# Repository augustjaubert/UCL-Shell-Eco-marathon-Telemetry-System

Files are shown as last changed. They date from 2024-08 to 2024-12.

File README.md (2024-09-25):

# UCL Shell Eco-marathon Telemetry System

This system is designed to record, store, and evaluate the performance of a the prototype in real-time and post-race.

A system user guide can be found [here](https://augusts-organization-4.gitbook.io/telemetry-system-handbook).

Fork this repository to iterate on it and continue building the telemetry system.

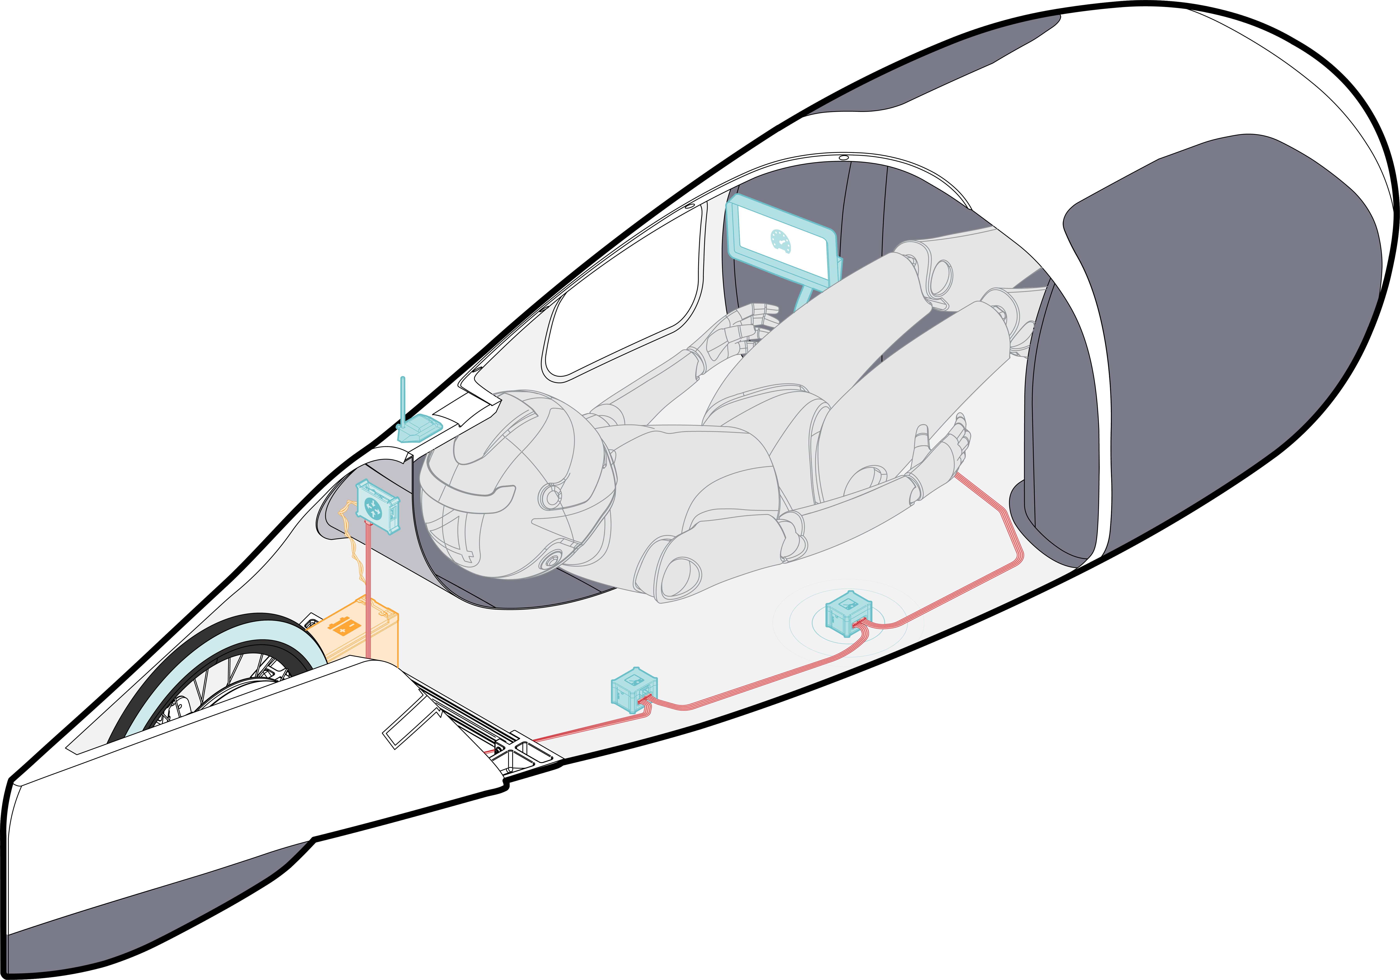
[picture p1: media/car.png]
System diagram


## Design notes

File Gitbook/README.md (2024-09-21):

# Overview

This user manual provides the information necessary for students to use the telemetry system.

<figure><figcaption></figcaption></figure>

### Features

This system was developed for usage on a race vehicle, to collect key performance indices. These vary depending on the vehicle competition, and this guide is directed towards the use on a vehicle participating in the Shell Eco Marathon competition.

It has,

* Expandable plug-in sensor capabilities
* CAN bus communication
* Data logging
* Live radio telemetry
* Driver & Race engineer graphical user interface

The system comprises of sensors, a receiver, and a radio station.

The sensors are configured as nodes on the CAN bus, meaning they each are paired with a small computer board. The latter acts as the middleman between the sensor’s interfacing protocol (i.e. the language the sensor talks in) and the CAN bus (i.e. what the telemetry system talks in).

The receiver is a computer board, who’s only function is to receive those sensor messages, store them onto a microSD card and handle the radio.

Notice that the receiver does not take care of the driver display. This is because depending on the setups, they may be at the complete opposite ends of a vehicle, so running a long cable from one to the other is not ideal. Instead, the system was designed so that any interfacing element (e.g. display, servo motor, etc.) can be attached to the CAN bus via a node and from there communicate with the system however it was programmed to.

The radio station is connected by USB to a computer, and all it does is intercept data over radio from the vehicle’s receiver, parse and translate that information, and then the computer program takes care of nicely displaying it all.

### Live race engineer interface

The live race engineer interface allows for the race engineer to assess the vehicle’s and driver’s performance during testing and at the race. This analysis is done via the use of plots. Currently there are three plots showing velocity, voltage, and current (these plots were meant to be used with a hydrogen powertrain). Besides the plots, there are toggle switches allowing for the comparison of various measured data (eg. Super-capacitor voltage and DC-DC voltage) and various laps.

The how to use section describes how the already existing application can be used for data analysis. While the how to edit/update section details how the application was setup and how to modify it or update it for future applications. Finally, the future work section mentions improvements that can be made.

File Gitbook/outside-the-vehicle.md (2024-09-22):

# Outside the vehicle

## Radio Station

### Setup

#### Hardware

1. Assembling the radio station with casing.
2. Attach the radio antenna to the station and USB connector to your laptop.

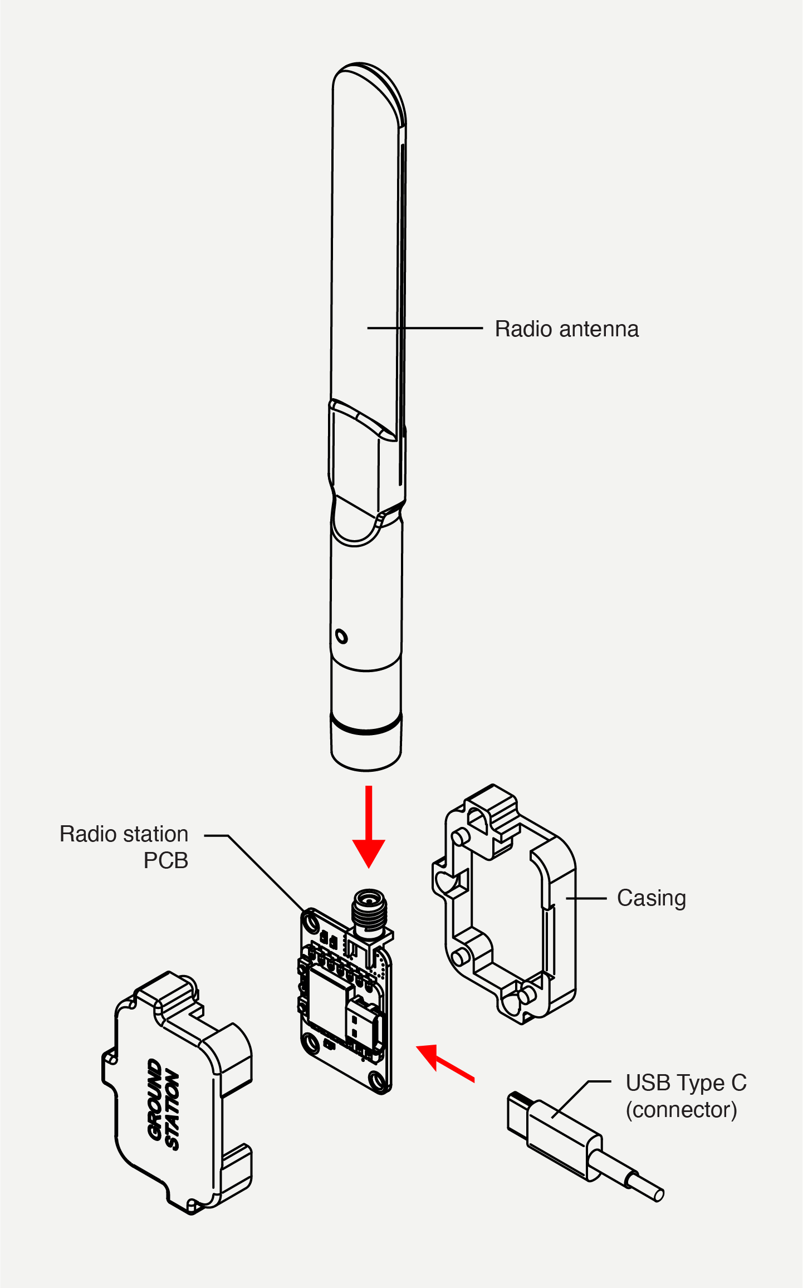
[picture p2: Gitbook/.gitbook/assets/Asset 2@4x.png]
<figure><figcaption></figcaption></figure>

#### Software

The radio station uses the Arduino IDE just like the other boards, and will need the RadioHead library installed from the github repository.

Before using the interface two applications need to be installed:

1\.        MATLAB for using the custom app.

2\.        VSCode (or any IDE) and the [Teleplot](https://github.com/nesnes/teleplot) extension installed for troubleshooting and redundancy.

### How to use

#### Software - Live Race Engineer Interface

1. Ensure that the telemetry system is turned on. Can be verified by lights on the boards and the driver display should be displaying information if connected.
2. Connect the ground station to your laptop.
3. Open Teleplot and select the port and baudrate (115200 by default).
4. Use the Teleplot interface to verify that data is being received and monitor it.
5. If Teleplot worked, disconnect from it (only one application can access a given serial port at a time) open the MATLAB application and run it.
6. On the top left of the MATLAB application select the port and baudrate (same as Teleplot).
7. If this worked successfully  you should be seeing data being plotted on the plots. Use the lap and quantity toggle switched to adjust the plots.

{% hint style="warning" %}
* Always start with Teleplot.
* The data that is being sent from the ground station to the laptop follows the format specified by Teleplot A:B§C
  * **A** is the name of the telemetry variable (be kind and avoid `:|` special chars in it!).
  * **B** is either the integer or floating point value to be plotted or a text format value to be displayed.
  * **C** is **optional** and is the unit of the telemetry ( please avoid `,;:|.` special chars in it!).
* The MATLAB application will crash if you click on a toggle switch that has no datafeed assigned to it.
* The timer in the MATLAB application currently needs to be started manually.
{% endhint %}

### Development

#### How to edit/update

The MATLAB application works by taking reading the next message from the serial port which contains a single measurement in the Teleplot format, identifying its quantity (eg. Velocity, Super-capacitor voltage), storing it to it’s corresponding cell array (an array of arrays more detail on it later), and updating the plots accordingly with the new data while also checking which checkbox is checked.

{% hint style="info" %}
**Why cell arrays?**

Cell arrays were used to allow for various measurements per lap to be taken and stored in a dynamic structure. Where the index of the cell array corresponds to the lap number. Allowing to compare various laps measurements with each other based on measurement number. Meaning that you can only compare for example the 10th velocity measurement of lap 3 with lap 5 and not the velocity at 100 m from the start line of these laps. This is a big negative of the current version of the interface, but assuming that the vehicle has consistent lap times then this approach is acceptable. How to improve this is detailed in the future work.
{% endhint %}

#### Main bits of the code

Whenever calling a function in the MATLAB app environmnent the first value you need to pass into it is always “app”.

<details>

<summary>Cell arrays</summary>

This is where the readings will be stored as discussed previously.

{% code overflow="wrap" %}
```matlab
velocity = {}; %Cell array to store velocity readings of each lap
current = {}; %Cell array to store current readings of each lap
voltage = {}; %Cell array to store voltage readings of each lap
%Voltage values
superCapsOverallVoltage = {}; %Cell array to store the supercaps overall voltage readings of each lap
beforeMotorControlVoltage = {}; %Cell array to store the before motor control voltage readings of each lap
DCDCVoltage = {}; %Cell array to store the DC DC voltage readings of each lap
```
{% endcode %}

</details>

<details>

<summary>Start-up function</summary>

This is the function that allows for the serial port readings to be continuously (= every 1 ms) monitored and updated (highlighted in yellow), ultimately enabling the plots to be updated. The other stuff named timer are used to update the stopwatch.

Define these in `properties (Access = private)`

<pre class="language-matlab" data-overflow="wrap"><code class="lang-matlab">        <a data-footnote-ref href="#user-content-fn-1">myTimer %Timer</a>
        Timer % Timer object
        TimerObject % Timer object
        StartTime % Start time
</code></pre>

Function itself

<pre class="language-matlab" data-overflow="wrap"><code class="lang-matlab">        function startupFcn(app)
            % Query available serial ports
            serialInfo = serialportlist("available");
            app.serialPort.Items = serialInfo;
            if isempty(serialInfo)
                app.serialPort.Items = {'No Ports Available'};
                app.serialPort.Enable = 'off';
            else
                app.serialPort.Enable = 'on';
            end
            <a data-footnote-ref href="#user-content-fn-2">app.myTimer = timer('ExecutionMode', 'fixedRate', 'Period', 1, 'TimerFcn', @(src, event)myTimerCallback(app, src, event)); % Specify the callback function</a>
            % Start the timer
            start(app.myTimer);
            app.TimerObject = timer(...
                'ExecutionMode', 'fixedRate', ...
                'Period', 1, ... % Update every second
                'TimerFcn', @(~,~)updateTimer(app));
        end
</code></pre>

</details>

As of now the way the code is setup you need to define a new add value function for each quantity that you want to be plotted and a function to update each of your plots.

<details>

<summary>Adding the new values</summary>

The function works by appending the value you give it to the end of the nth array in the cell array. Where n is the current lap number.

{% code overflow="wrap" %}
```matlab
        function addVelocityValue(app, value)
            lapIndex = app.LapField.Value; % Get the current lap index from the LapField
    
            if length(app.velocity) < lapIndex || isempty(app.velocity{lapIndex})
                % If the current lap's cell doesn't exist, initialize it with the value
                app.velocity{lapIndex} = value;
            else
                % Otherwise, append the value to the existing cell data
                app.velocity{lapIndex} = [app.velocity{lapIndex}, value];
            end
        end
```
{% endcode %}

</details>

<details>

<summary>Plotting the new values</summary>

_Single variable plots_ - For plots like velocity where you are only comparing its value through various laps the following function was created to plot it.

{% code overflow="wrap" %}
```matlab
        function updateVelocityPlot(app)
            cla(app.velUIAxes);  % Clear the current axes
            hold(app.velUIAxes, 'on');
            checkedNodes = app.LapTree.CheckedNodes;  % Get the list of checked nodes

            % Loop over each checked node
            for i = 1:numel(checkedNodes)
                node = checkedNodes(i);  % Get each checked node
                lapIndex = node.NodeData;  % Assuming NodeData stores the corresponding lap index

                % Ensure lapIndex is valid and within bounds
                if isnumeric(lapIndex) && lapIndex > 0 && lapIndex <= length(app.velocity)
                    % Check if the lap data exists and is not empty
                    if ~isempty(app.velocity{lapIndex})
                        plot(app.velUIAxes, app.velocity{lapIndex}, 'DisplayName', sprintf('Lap %d', lapIndex), 'LineWidth',4);
                    end
                end
            end
            hold(app.velUIAxes, 'off');
            legend(app.velUIAxes, 'Location', 'best');
            title(app.velUIAxes, 'Velocity vs Measurements');
            xlabel(app.velUIAxes, 'Measurements');
            ylabel(app.velUIAxes, 'Velocity (m/s)');
        end

```
{% endcode %}

***

_Multivariable plots_ - For plots where multiple quantities are being compared within a lap and over various laps the following function can be used. With the difference compared to the previous function being the switch which checks for which quantities should be plotted for the given lap.

{% code overflow="wrap" %}
```matlab
        function updateCurrentPlot(app)
            cla(app.currentUIAxes);  % Clear the current axes
            hold(app.currentUIAxes, 'on');
            checkedLapNodes = app.LapTree.CheckedNodes;  % Get the list of checked nodes from the LapTree
            checkedCurrentParameters = app.CurrentTree.CheckedNodes;  % Get the list of checked voltage parameters

            % Loop over each checked lap node
            for i = 1:numel(checkedLapNodes)
                lapNode = checkedLapNodes(i);  % Get each checked lap node
                lapIndex = lapNode.NodeData;  % Assuming NodeData stores the corresponding lap index

                % Ensure lapIndex is valid and within bounds
                if isnumeric(lapIndex) && lapIndex > 0 && lapIndex <= length(app.velocity)
                    % Check if the lap data exists and is not empty

                    % Loop over each checked parameter node
                    for j = 1:numel(checkedCurrentParameters)
                        parameterNode = checkedCurrentParameters(j);
                        parameterIndex = parameterNode.NodeData;  % NodeData here should correspond to the parameter index

                        switch parameterIndex
                            case 1  % Supercaps Overall Current
                                if ~isempty(app.superCapsOverallCurrent{lapIndex})
                                    plot(app.currentUIAxes, str2double(app.superCapsOverallCurrent{lapIndex}), 'DisplayName', sprintf('SCO Lap %d', lapIndex), 'LineWidth',4);
                                end
                            case 2  % Supercaps Charge Current
                                if ~isempty(app.superCapsChargeCurrent{lapIndex})
                                    plot(app.currentUIAxes, str2double(app.superCapsChargeCurrent{lapIndex}), 'DisplayName', sprintf('SCC Lap %d', lapIndex), 'LineWidth',4);
                                end
                            case 3  % Before Motor Control Current
                                if ~isempty(app.beforeMotorControlCurrent{lapIndex})
                                    plot(app.currentUIAxes, str2double(app.beforeMotorControlCurrent{lapIndex}), 'DisplayName', sprintf('BMC Lap %d', lapIndex), 'LineWidth',4);
                                end
                            % case 4  % DC DC Current
                            %     if ~isempty(app.DCDCCurrent{lapIndex})
                            %         plot(app.currentUIAxes, str2double(app.DCDCCurrent{lapIndex}), 'DisplayName', sprintf('DCDC Lap %d', lapIndex), 'LineWidth',4);
                            %     end
                        end
                    end
                end
            end
            hold(app.currentUIAxes, 'off');
            legend(app.currentUIAxes, 'Location', 'best');
            title(app.currentUIAxes, 'Current vs Measurements');
            xlabel(app.currentUIAxes, 'Measurements');
            ylabel(app.currentUIAxes, 'Current (A)');
        end
```
{% endcode %}

</details>

#### Putting it all together

{% hint style="info" %}
You can click on the underlined code to reveal information about its use.
{% endhint %}

<pre class="language-matlab" data-overflow="wrap" data-line-numbers data-full-width="true"><code class="lang-matlab"><a data-footnote-ref href="#user-content-fn-3">function myTimerCallback(app, src, event)</a>
            <a data-footnote-ref href="#user-content-fn-4">if (src.NumBytesAvailable > 0)</a>
                        <a data-footnote-ref href="#user-content-fn-5">dataStr = readline(src);  % Reads data from the serial port until a newline is received</a>
                        % Remove non-ASCII characters except '§'
                        <a data-footnote-ref href="#user-content-fn-6">dataStr = regexprep(dataStr, '[\s>]|[^\x20-\x7E§]', '');</a>
                        <a data-footnote-ref href="#user-content-fn-7">try</a>
                            % Split the data into its components
                            <a data-footnote-ref href="#user-content-fn-8">splitData = strsplit(dataStr, '§');  % Split based on the '§' delimiter</a>
                            <a data-footnote-ref href="#user-content-fn-9">if numel(splitData) == 2</a>
                                <a data-footnote-ref href="#user-content-fn-10">varNameValue = splitData{1};</a>
                                %varUnit = splitData{2};

                                % Further split to separate variable name and value
                                <a data-footnote-ref href="#user-content-fn-11">nameValueSplit = strsplit(varNameValue, ':');</a>
                                    <a data-footnote-ref href="#user-content-fn-12">if numel(nameValueSplit) == 2</a>
                                        <a data-footnote-ref href="#user-content-fn-13">varName = nameValueSplit{1};</a>
                                        <a data-footnote-ref href="#user-content-fn-14">varValue = str2double(nameValueSplit{2});  % Convert value to double</a>

                                        <a data-footnote-ref href="#user-content-fn-15">if strcmp(varName, 'Lap#')</a>
                                            <a data-footnote-ref href="#user-content-fn-16">app.LapField.Value = varValue;</a>
                                            <a data-footnote-ref href="#user-content-fn-17">handleNewLap(app);</a>

                                        elseif strcmp(varName, 'Velocity')
                                            %disp('This is a velocity reading');
                                            <a data-footnote-ref href="#user-content-fn-18">addVelocityValue(app, varValue);</a>
                                            <a data-footnote-ref href="#user-content-fn-19">updateVelocityPlot(app);</a>

                                        %Supercaps Overall voltage update
                                        elseif strcmp(varName, 'SCOV')
                                            <a data-footnote-ref href="#user-content-fn-20">addSCOVoltageValue(app, string(varValue));</a>
                                            <a data-footnote-ref href="#user-content-fn-21">updateVoltagePlot(app);</a>

                                        %before motor control voltage update
                                        elseif strcmp(varName, 'BMCV')
                                            <a data-footnote-ref href="#user-content-fn-22">addBMCVoltageValue(app, string(varValue));</a>
                                            <a data-footnote-ref href="#user-content-fn-23">updateVoltagePlot(app);</a>

                                        %DC DC voltage update
                                        elseif strcmp(varName, 'DCDCV')
                                            <a data-footnote-ref href="#user-content-fn-24">addDCDCVoltageValue(app, string(varValue));</a>
                                            <a data-footnote-ref href="#user-content-fn-25">updateVoltagePlot(app);</a>

                                        %Supercaps Overall current update
                                        elseif strcmp(varName, 'Curr1')
                                            <a data-footnote-ref href="#user-content-fn-26">addSCOCurrentValue(app, string(varValue));</a>
                                            <a data-footnote-ref href="#user-content-fn-27">updateCurrentPlot(app);</a>

                                        %Supercaps Charge current update
                                        elseif strcmp(varName, 'Curr2')
                                            <a data-footnote-ref href="#user-content-fn-28">addSCCCurrentValue(app, string(varValue));</a>
                                            <a data-footnote-ref href="#user-content-fn-29">updateCurrentPlot(app);</a>

                                        %Before Motor Control Current
                                        %update
                                        elseif strcmp(varName, 'Curr3')
                                            <a data-footnote-ref href="#user-content-fn-30">addBMCCurrentValue(app, string(varValue));</a>
                                            <a data-footnote-ref href="#user-content-fn-31">updateCurrentPlot(app);</a>

                                        %DC DC Current update
                                        elseif strcmp(varName, 'DCDCC')
                                            <a data-footnote-ref href="#user-content-fn-32">addDCDCCurrentValue(app, string(varValue));</a>
                                            <a data-footnote-ref href="#user-content-fn-33">updateCurrentPlot(app);</a>
                                        end
                                    else
                                        disp('Error: Variable name and value not in expected format.');
                                    end
                            else
                                    disp('Error: Data not in expected format.');
                            end
                        catch
                            disp(['Error processing data: ', dataStr]);
                        end
            end
        end
</code></pre>

### Future work

#### Live Race Engineer Interface

The interface can be improved upon by creating a sophisticated database structure and querying the data from it. This would allow for any kind of comparison plot to be created. Furthermore, instead of sending the measurements from the vehicle to the ground station they could be uploaded to an online database from which the readings can be accessed by any number of race engineers and from anywhere, allowing more people to do various kinds of data analysis simultaneously.

## Off-track data analysis

The following procedure applies to both hydrogen and battery electric MATLAB code, found on the Github repo.&#x20;

The code first runs an overview of the testing data with the lap-by-lap performance. Then, the user inputs the lap numbers to allow for comparison of laps. Using the battery testing data, the tyre analysis can be performed automatically afterwards.&#x20;

The hydrogen powertrain introduces further losses which I have not been able to estimate accordingly. In case of Hydrogen analysis, Milan can perform some simulations. His results can be plotted using the MilanPlots.mlx file.

Hydrogen and Battery Analysis Procedure:

1. Gather the testing data in excel and format it using the column order specific to each analysis. For this, please check the excel tables provided and match the title of the columns with the raw data from testing.

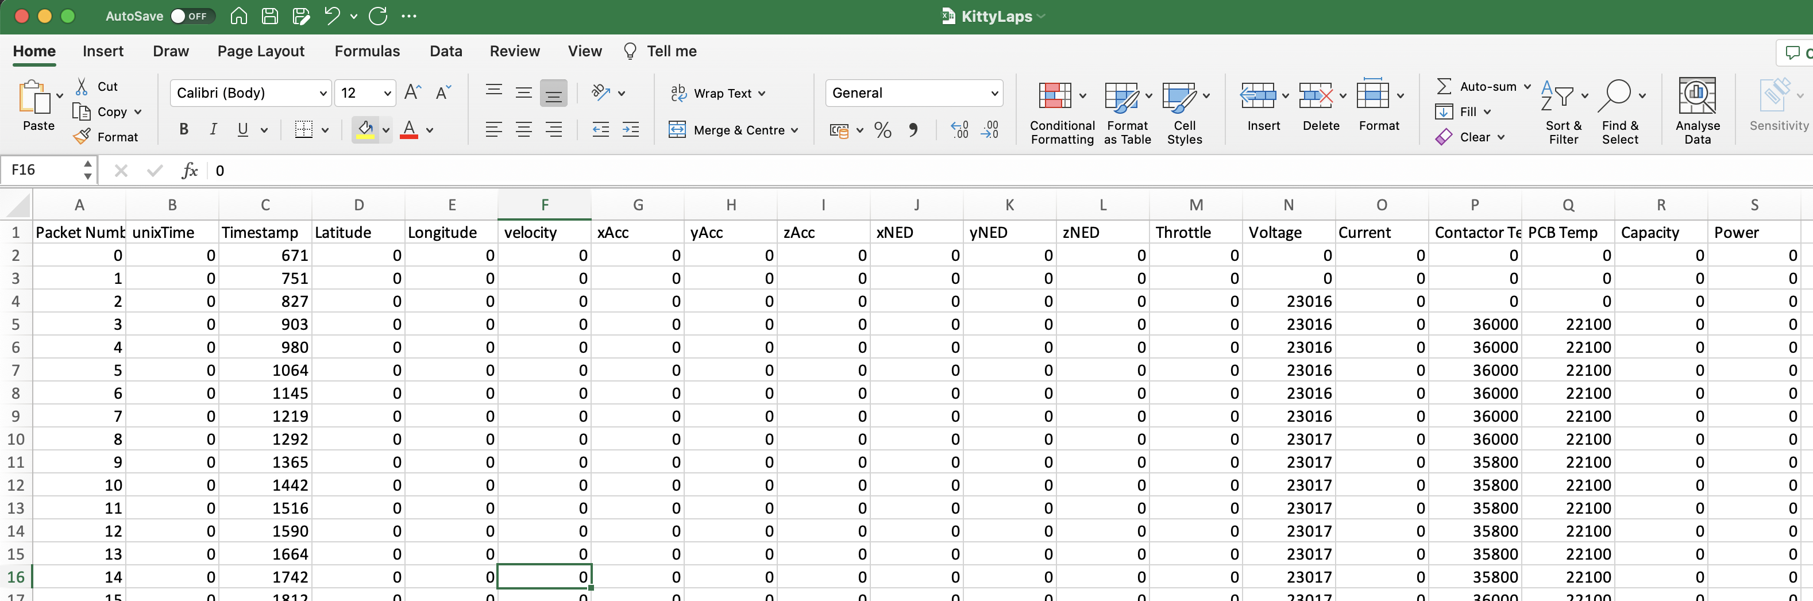
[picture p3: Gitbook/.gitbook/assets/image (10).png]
<figure><figcaption><p>Example of an excel sheet with telemetry data columns.</p></figcaption></figure>

{% hint style="info" %}
This data arrangement was specifically made for a hydrogen powertrain with the sensor mentioned in the [2024 configuration section](in-the-vehicle.md#id-2024-configuration).

If you are changing the sensors, you will need to modify the MATLAB code to account for that. Another (future work) solution is to make the plotting of the data automatic where if you upload a folder sectioned into multiple sensor folders from the receiver SD card,

e.g.&#x20;

* config (folder)
  * README.txt
* sensor 1 (folder)
  * telemetry\_date\_time.txt
* sensor 2 (folder)
  * telemetry\_date\_time.txt

... then the program will detect and plot a graph for each sensor folder.
{% endhint %}

2. Choose either the hydrogen or the electrical battery MATLAB code for analysis. In the first few lines, change the command to fit the correct file name: data = readtable('RandomName.xlsx');
3. Follow the command window and input the two lap numbers to allow for the comparison of laps.
4. All the results are now displayed. The next step is to run Milan Plots or the Tyre Analysis.

[^1]: A

[^2]: A

[^3]: Timer function callback, allows the plots to be continuously updated.

[^4]: Converts the Teleplot formatted measurement into VarName and VarValue.

[^5]: Converts the Teleplot formatted measurement into VarName and VarValue.

[^6]: Converts the Teleplot formatted measurement into VarName and VarValue.

[^7]: Converts the Teleplot formatted measurement into VarName and VarValue.

[^8]: Converts the Teleplot formatted measurement into VarName and VarValue.

[^9]: Converts the Teleplot formatted measurement into VarName and VarValue.

[^10]: Converts the Teleplot formatted measurement into VarName and VarValue.

[^11]: Converts the Teleplot formatted measurement into VarName and VarValue.

[^12]: Converts the Teleplot formatted measurement into VarName and VarValue.

[^13]: Converts the Teleplot formatted measurement into VarName and VarValue.

[^14]: Converts the Teleplot formatted measurement into VarName and VarValue.

[^15]: Checks whether VarName is “Lap#” and if so increments to lap number.

[^16]: Checks whether VarName is “Lap#” and if so increments to lap number.

[^17]: Checks whether VarName is “Lap#” and if so increments to lap number.

[^18]: Compares the VarName with the a predefined variable name and stores it VarValue to the corresponding cell array.

[^19]: Updates the plots.

[^20]: Compares the VarName with the a predefined variable name and stores it VarValue to the corresponding cell array.

[^21]: Updates the plots.

[^22]: Compares the VarName with the a predefined variable name and stores it VarValue to the corresponding cell array.

[^23]: Updates the plots.

[^24]: Compares the VarName with the a predefined variable name and stores it VarValue to the corresponding cell array.

[^25]: Updates the plots.

[^26]: Compares the VarName with the a predefined variable name and stores it VarValue to the corresponding cell array.

[^27]: Updates the plots.

[^28]: Compares the VarName with the a predefined variable name and stores it VarValue to the corresponding cell array.

[^29]: Updates the plots.

[^30]: Compares the VarName with the a predefined variable name and stores it VarValue to the corresponding cell array.

[^31]: Updates the plots.

[^32]: Compares the VarName with the a predefined variable name and stores it VarValue to the corresponding cell array.

[^33]: Updates the plots.

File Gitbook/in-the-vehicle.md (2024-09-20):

# In the vehicle

## Node

The sensors are configured as nodes on the CAN bus, meaning they each are paired with a small computer board. The latter acts as the middleman between the sensor’s interfacing protocol (i.e. the language the sensor talks in) and the CAN bus (i.e. what the telemetry system talks in).

The node computer hardware diagram is presented in the figure below.

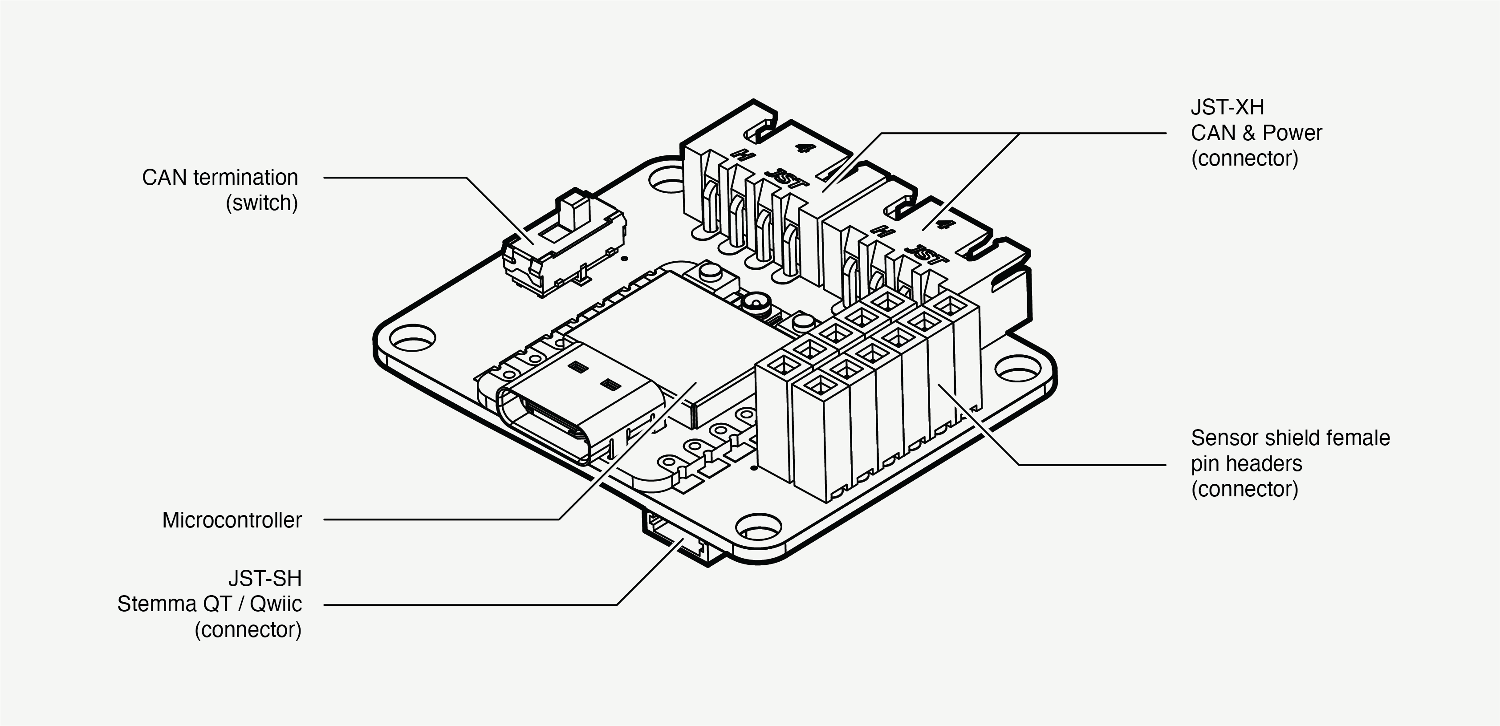
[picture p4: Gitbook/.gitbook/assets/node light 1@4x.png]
<figure><picture><source srcset=".gitbook/assets/node dark 1@4x.png" media="(prefers-color-scheme: dark)"></picture><figcaption></figcaption></figure>

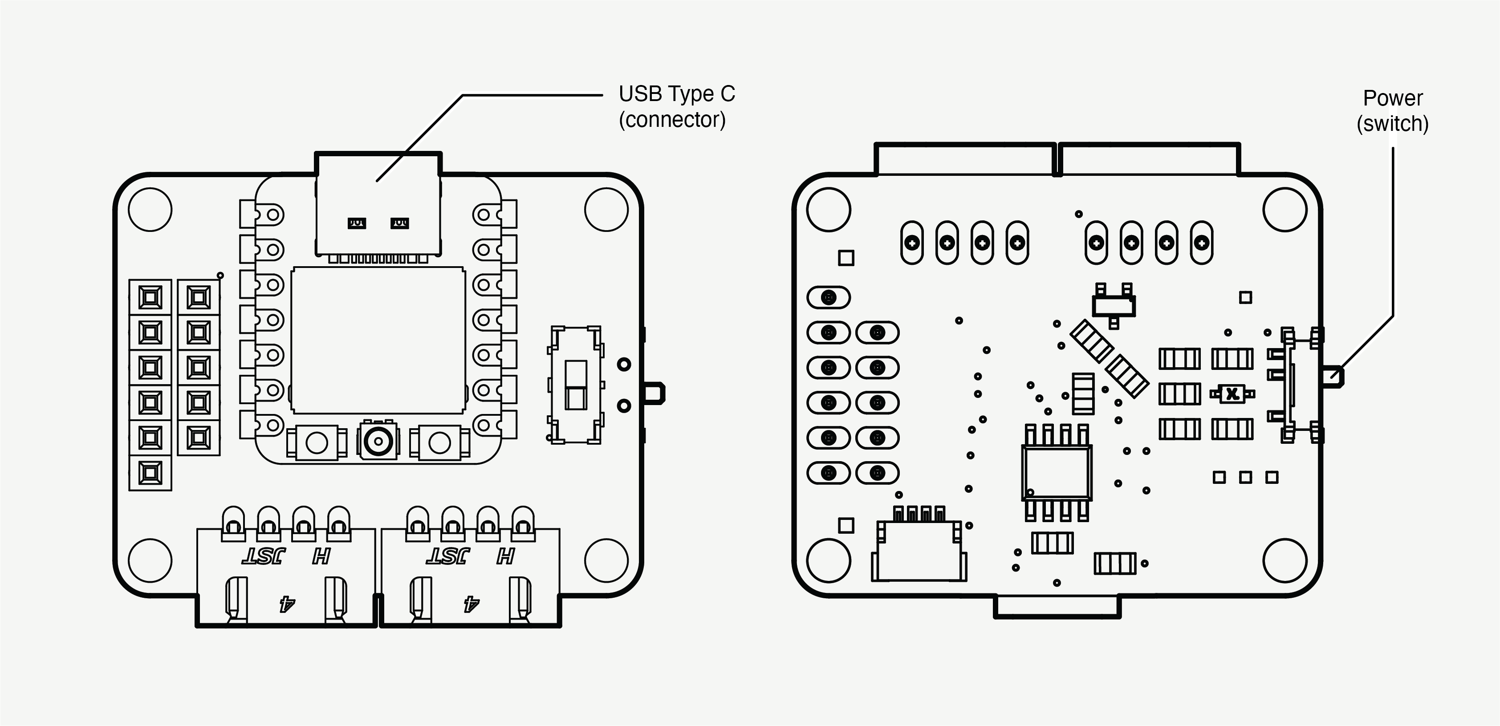
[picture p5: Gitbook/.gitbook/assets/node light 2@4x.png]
<figure><picture><source srcset=".gitbook/assets/node dark 2@4x.png" media="(prefers-color-scheme: dark)"></picture><figcaption><p>Technical diagrams of the node computer</p></figcaption></figure>

### Technical specs

{% tabs %}
{% tab title="Tech specs" %}
* The nodes use a ESP32 microcontroller (S3 or C3 models) from Espressif, manufactured by Seeed ([XIAO ESP32C3](https://wiki.seeedstudio.com/XIAO\_ESP32C3\_Getting\_Started/) / [XIAO ESP32S3](https://wiki.seeedstudio.com/xiao\_esp32s3\_getting\_started/)) (top surface).
* It uses two rows of 6 and 5 female headers (top surface) to connect to the sensor shield.
* A Qwiic / Stemma QT connector to connect to sensor breakout boards directly (no shield).
* They are equipped with [TCAN1462V-Q1](https://www.ti.com/lit/ds/symlink/tcan1462-q1.pdf?HQS=dis-mous-null-mousermode-dsf-pf-null-wwe\&ts=1698833597358) CAN transceivers (bottom surface) that make use of the MCU’s native [TWAI](https://docs.espressif.com/projects/esp-idf/en/stable/esp32/api-reference/peripherals/twai.html#overview) controllers.
* They have two daisy-chained 4-pin JST XH connectors (top surface) for the data transmission CAN High / Low, and the power pins from the Receiver +5V and GND.
* The slide switch on the top surface is the CAN termination switch, connecting the CAN High and Low lines by a 120 Ohm resistor.
* The CAN lines also have footprint for capacitors in series and parallel (bottom surface) to help if filtering is needed on the bus.
{% endtab %}

{% tab title="Pinout" %}
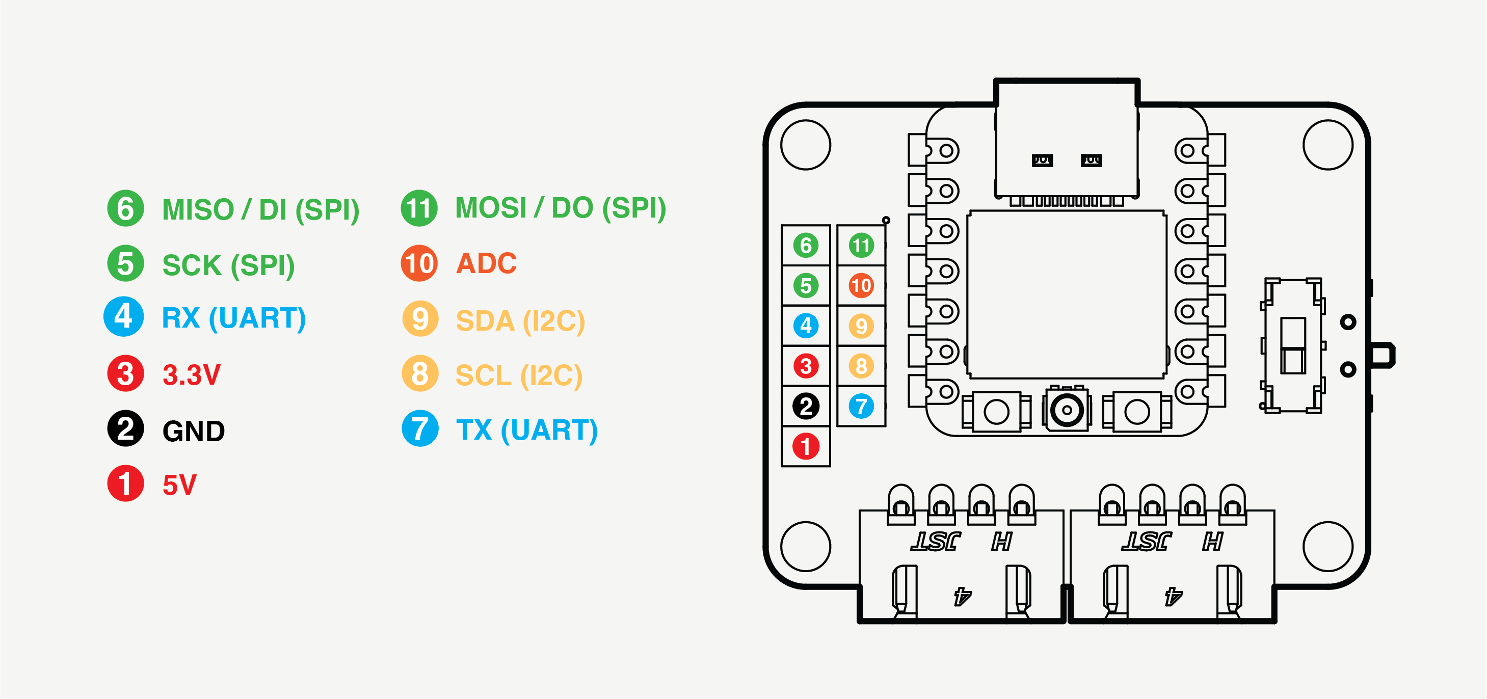
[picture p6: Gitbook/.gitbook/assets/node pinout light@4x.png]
<figure><figcaption></figcaption></figure>

{% hint style="info" %}
This pinout diagram is valid for the XIAO ESP32-C3 microcontrollers, but some pins also double as analog pins on the XIAO ESP32-S3 (see Table 1), marked as A\<Number> (e.g. A5).
{% endhint %}

<table><thead><tr><th width="154">pin #</th><th>C3 pinout</th><th>S3 pinout</th></tr></thead><tbody><tr><td>1</td><td>5V</td><td>5V</td></tr><tr><td>2</td><td>GND</td><td>GND</td></tr><tr><td>3</td><td>3.3V</td><td>3.3V</td></tr><tr><td>4</td><td>D7 / RX / GPIO20</td><td>D7 / RX / GPIO44</td></tr><tr><td>5</td><td>D8 / SCK / GPIO8</td><td>D8 / A8 / SCK / GPIO7</td></tr><tr><td>6</td><td>D9 / MISO / GPIO9</td><td>D9 / A9 / MISO / GPIO8</td></tr><tr><td>7</td><td>D6 / TX / GPIO21</td><td>D6 / TX / GPIO43</td></tr><tr><td>8</td><td>D5 / SCL / GPIO7</td><td>D5 / A5 / SCL / GPIO6</td></tr><tr><td>9</td><td>D4 / SDA / GPIO6</td><td>D4 / A4 / SDA / GPIO5</td></tr><tr><td>10</td><td>D3 / A3 / GPIO5</td><td>D3 / A3 / GPIO4</td></tr><tr><td>11</td><td>D10 / MOSI / GPIO10</td><td>D10 / A10 / MOSI / GPIO9</td></tr><tr><td>CAN_TX</td><td>GPIO_NUM_3</td><td>GPIO_NUM_2</td></tr><tr><td>CAN_RX</td><td>GPIO_NUM_4</td><td>GPIO_NUM_3</td></tr><tr><td>CAN_Standby</td><td>GPIO2</td><td>GPIO1</td></tr></tbody></table>
{% endtab %}
{% endtabs %}

### Setup

#### Hardware

1. Assembling the node case (in ascending order)

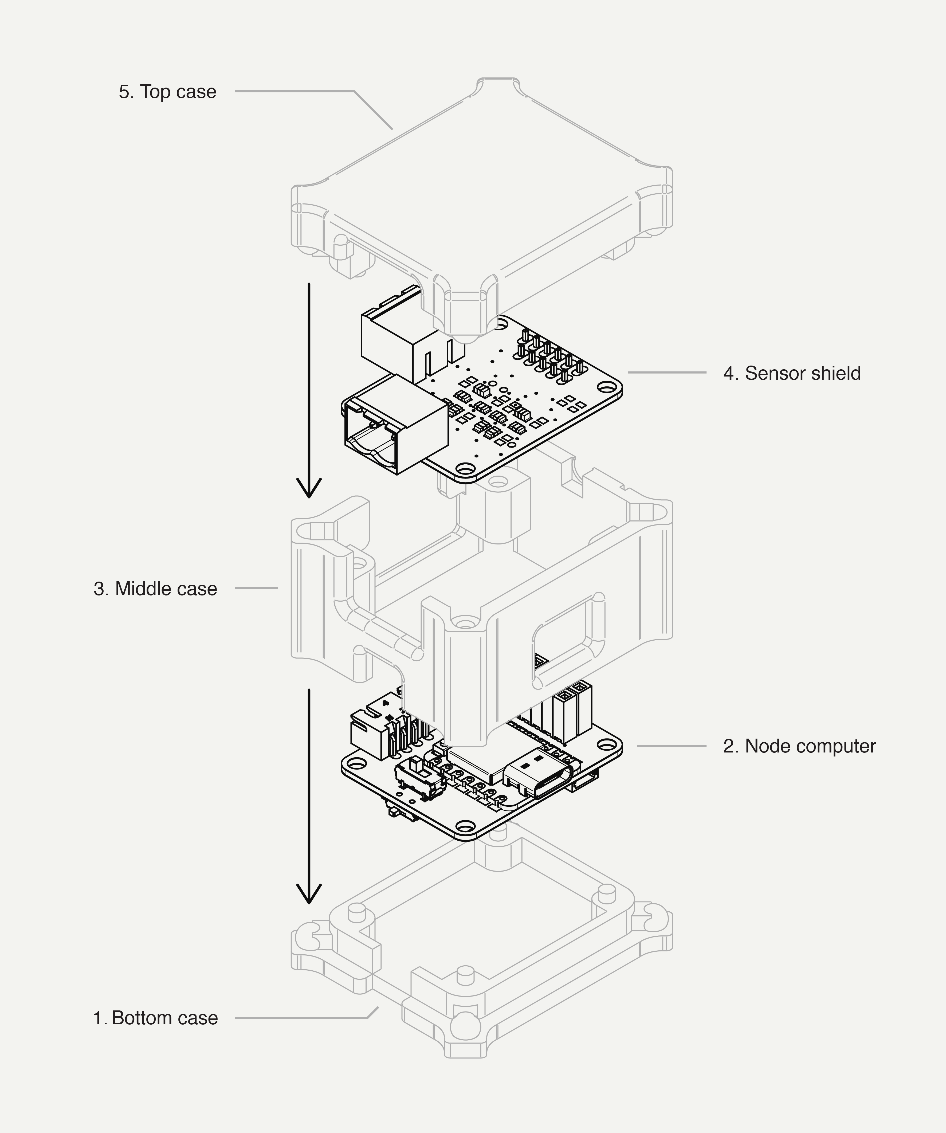
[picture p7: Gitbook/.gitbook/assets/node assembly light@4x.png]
<figure><figcaption></figcaption></figure>

{% hint style="info" %}
You can also connect sensor breakout boards that feature a Qwiic or Stemma QT connector from Adafruit and Sparkfun directly to the similar connector on the bottom surface. This is the case for the GPS node, which uses a Sparkfun breakout board.
{% endhint %}

2. Attaching the node to the CAN/Power bus

Connecting to the CAN and Power bus is easy. There are two 4-pin JST XH connectors opposite to the USB-C connector, which are connected in parallel for you to daisy-chain the whole system. This means that there’s no wrong way to connect it, just attach one cable to the bus, and if you want to add a new sensor, just attach another cable in the other connector and into the new node.

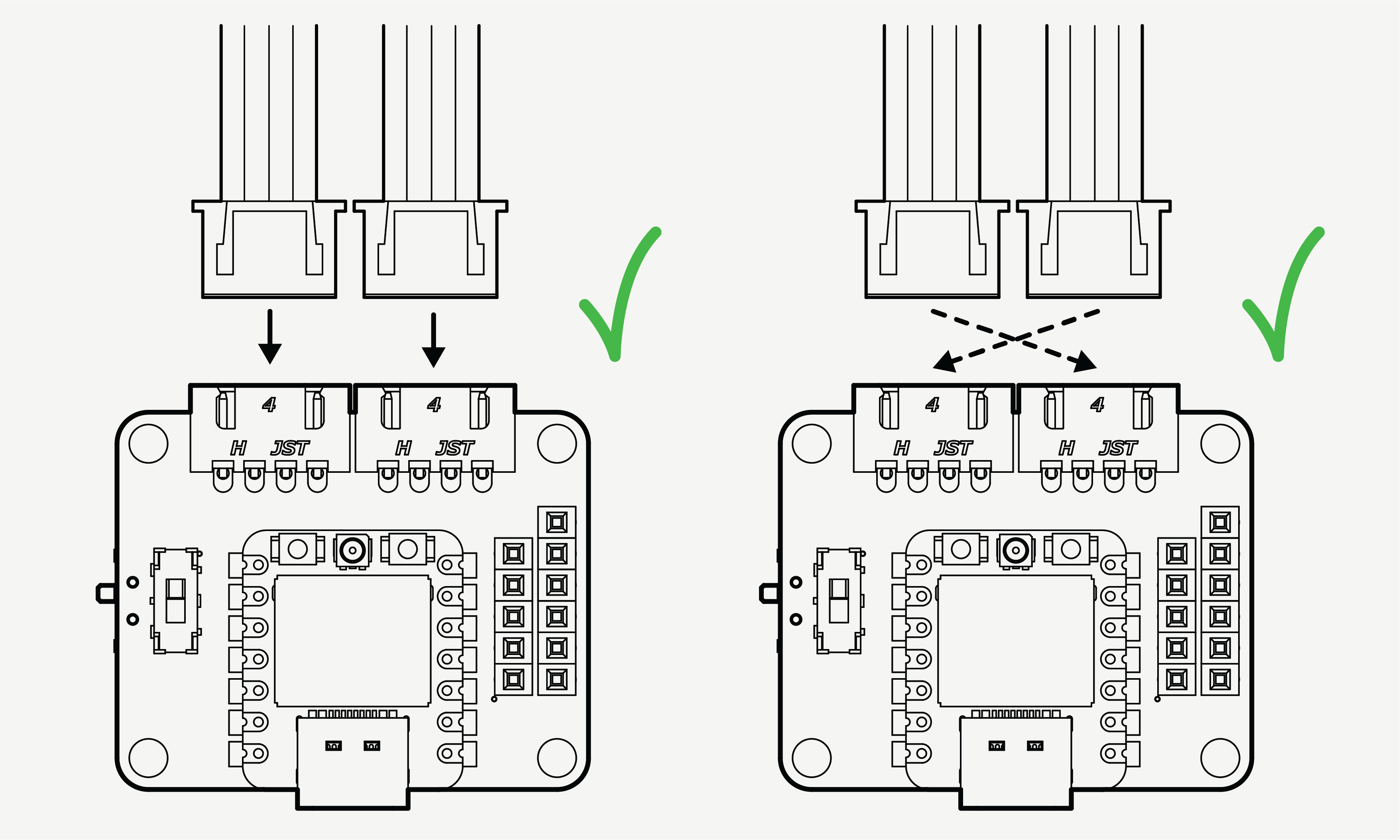
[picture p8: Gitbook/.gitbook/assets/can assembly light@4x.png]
<figure><picture><source srcset=".gitbook/assets/can assembly dark@4x.png" media="(prefers-color-scheme: dark)"></picture><figcaption></figcaption></figure>

3. Installing in the vehicle

Place the node wherever it is needed in the vehicle.

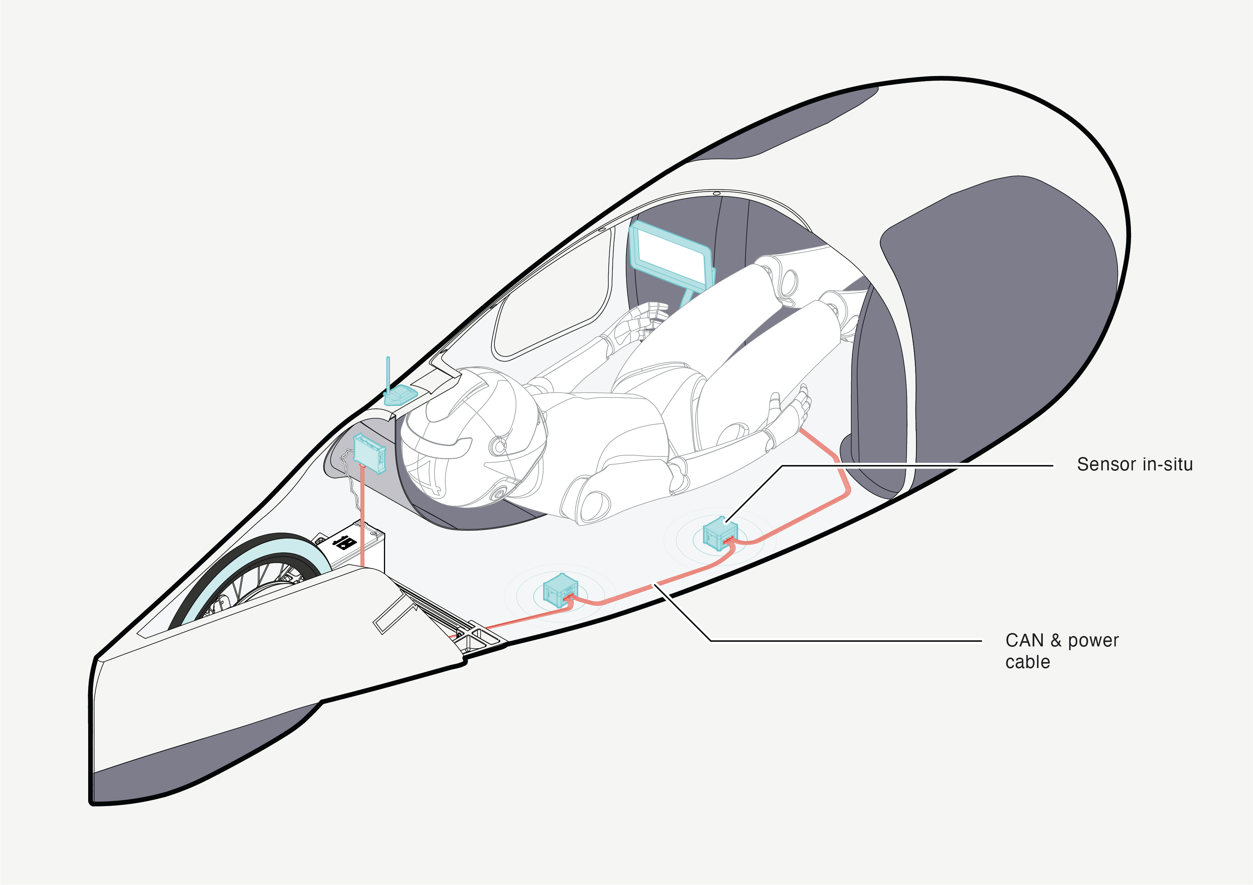
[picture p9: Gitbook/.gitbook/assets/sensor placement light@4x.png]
<figure><figcaption></figcaption></figure>

{% hint style="info" %}
If you need to make a new cable, make sure to use the proper connections as seen in the figure below.
{% endhint %}

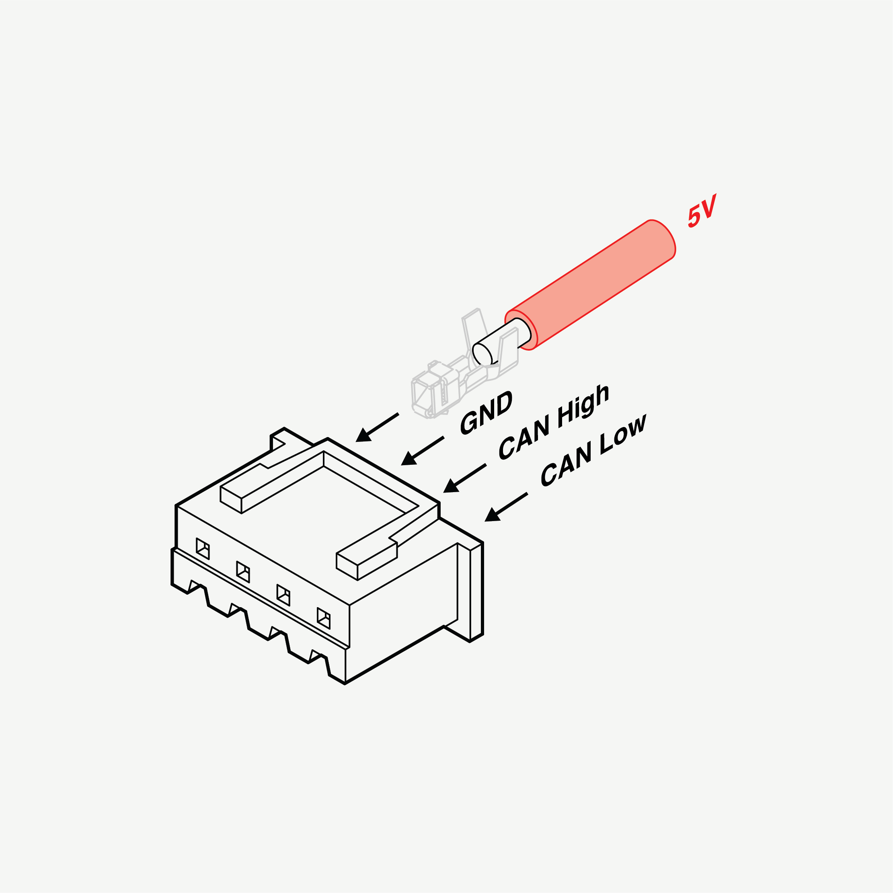
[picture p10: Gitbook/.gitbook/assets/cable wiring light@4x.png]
<figure><picture><source srcset=".gitbook/assets/cable wiring dark@4x.png" media="(prefers-color-scheme: dark)"></picture><figcaption><p>CAN &#x26; Power cable wiring diagram</p></figcaption></figure>

#### Software

1. Installing the integrated development environment (IDE)

The system works similar to most Arduino projects, as it has been coded in C++ using the Arduino IDE.

Any IDE will do the job, however we recommend using the following:

[Arduino IDE](https://www.arduino.cc/en/software) <mark style="color:orange;">is the easiest to use, has plenty of documentation and forum help and is sufficient almost 99% of the time.</mark>

[Platform IO](https://platformio.org/) (through VSCode) is essentially a pro version, where you have more control but requires a manual setup.

[ESP-IDF](https://docs.espressif.com/projects/esp-idf/en/stable/esp32/get-started/index.html#introduction) is the MCU's native IDE, which gives more liberty in using all its functions.

2. ESP board definitions

The ESP boards (MCU) are not defined by default in the Arduino IDE. You will have to add them initially to be able to connect to the nodes and others.

To do this in the Arduino IDE, navigate to **File > Preferences**, and fill **"Additional Boards Manager URLs"** with the url below: [_https://raw.githubusercontent.com/espressif/arduino-esp32/gh-pages/package\_esp32\_index.json_](https://raw.githubusercontent.com/espressif/arduino-esp32/gh-pages/package\_esp32\_index.json)

Navigate to **Tools > Board > Boards Manager...**, type the keyword "**esp32**" in the search box, select the latest version of **esp32**, and install it.

3. Installing the node library

Download the two files `Node.h` and `Node.cpp` from the [Github repository](https://github.com/augustjaubert/UCL-SEM-Telemetry-System) in the Node folder.

To add the node library to your arduino sketch[^1], simply add the two files in your sketch folder.

<details>

<summary>Example folder organisation</summary>

```
example_sketch (folder)
-> Node.cpp
-> Node.h
-> example_sketch.ino (arduino sketch)
```

</details>

4. Connecting to the node computer board

To connect the node computer to the arduino sketch, select the top-left text box **Select Board**.

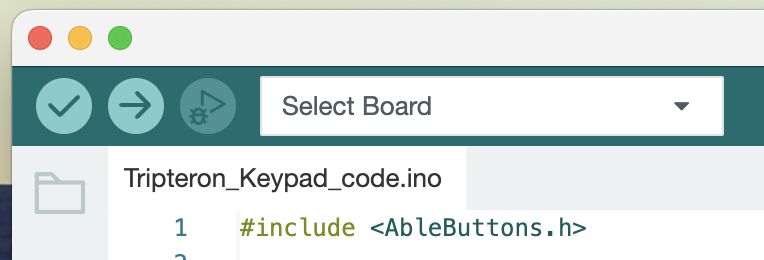
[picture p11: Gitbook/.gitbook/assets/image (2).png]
<figure><figcaption></figcaption></figure>

For C3 models - XIAO\_ESP32C3

For S3 models - XIAO\_ESP32S3

### How to use

Find the quick guide in the [overview section](./#quick-installation-guide).

{% hint style="info" %}
You can add up to 70+ nodes onto the CAN bus, however limiting the number of sensors to <15 is recommended (i.e. limit the different messages competing on the CAN bus).
{% endhint %}

#### Steps

1. Switch the node ON.

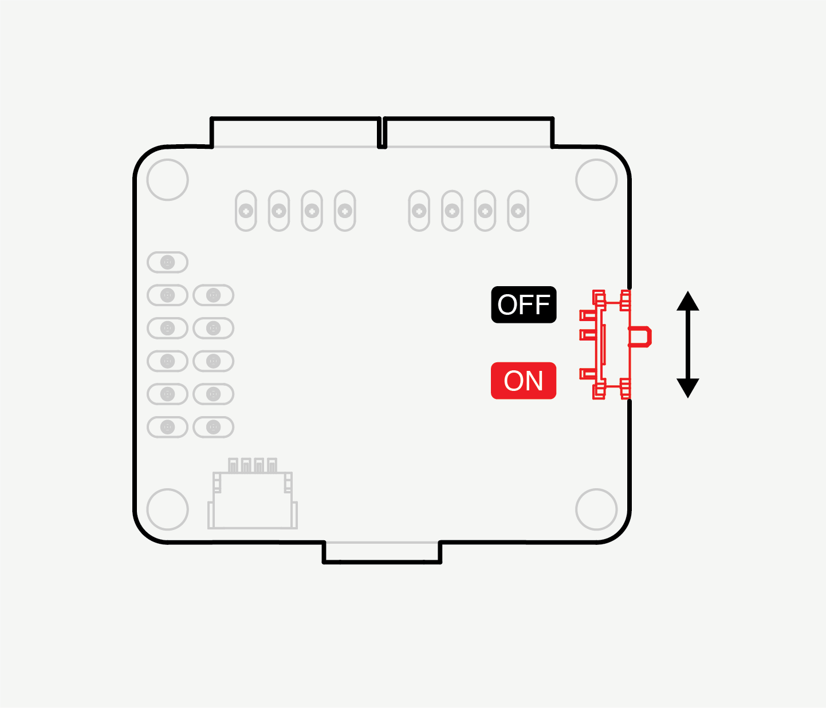
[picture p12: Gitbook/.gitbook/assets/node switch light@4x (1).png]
<figure><figcaption></figcaption></figure>

2. Assemble the node (sensor, computer and case).
3. Connect a CAN cable to one of the JST sockets to add the node on the CAN bus.
4. If the node is added at the end of the bus, switch the CAN termination ON<mark style="color:orange;">.</mark>

{% hint style="info" %}
After the system is powered, the node is powered if you see a LED lighting up.
{% endhint %}

{% hint style="warning" %}
Later versions of the node computer boards have a slide switch on the bottom, which need to be activated for the power rail to go through the board.&#x20;

Be careful because earlier versions have reversed ON/OFF writings by mistake, so if in doubt test it outside the vehicle, and if you see a blinking red/yellow light coming from the node, it is powered.
{% endhint %}

#### Troubleshooting

If it seems as though the Receiver is not seeing the sensor messages, or something else is not working as it should:

1. Disassemble the node.
2. Connect the node computer to your laptop through USB.
3. Open Arduino IDE, and check that you have the correct board definition in the top-left text box **Select Board**.

<figure><figcaption></figcaption></figure>

<details>

<summary>No board appearing</summary>

If you don't see a board appearing, then the MCU is not powered, or the serial connection has been severed. This can be because,

* The USB cable is not properly connected either to the node or laptop
* The MCU is not receiving power, which can be checked with a multimeter on the MCU pins to see if it detects a voltage. This can be due to a severed power connection on the circuit.
* The serial connection is severed, which can be because&#x20;
  * the USB connector on the MCU has been damaged,&#x20;
  * or because something (e.g. static electricity) has caused your laptop to disconnect the USB port (safety mode). It happens that connection is re-established after some time.
    * You can first try to reset the board by clicking the **RESET BUTTON** once while the board is connected to your PC. If that does not work, hold the **BOOT BUTTON**, connect the board to your PC while holding the **BOOT** button, and then release it to enter **bootloader mode**.

</details>

<details>

<summary>The wrong board is appearing</summary>

If the wrong board is appearing, that is a good sign because it recognises something.

You can open the text box, click on select **other board and port...** and search for the appropriate board.

The boards are,

For C3 models - XIAO\_ESP32C3

For S3 models - XIAO\_ESP32S3

S3 models are identifiable by the writing on the sticker and the presence of solderable pins on the bottom, as seen on the right side of the image below.

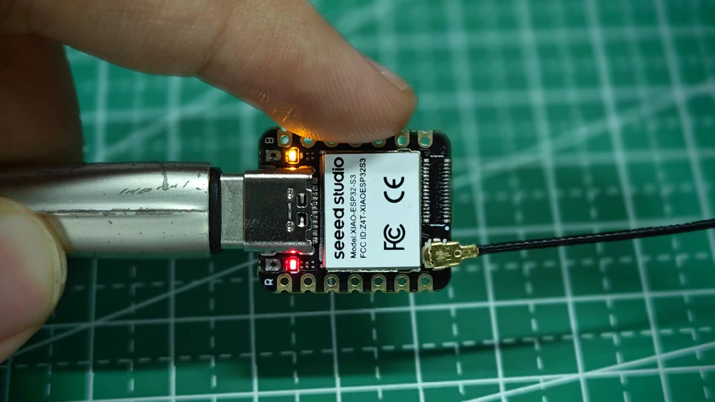
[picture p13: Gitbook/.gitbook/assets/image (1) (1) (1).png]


</details>

4. Open the serial monitor, in the top-right corner.

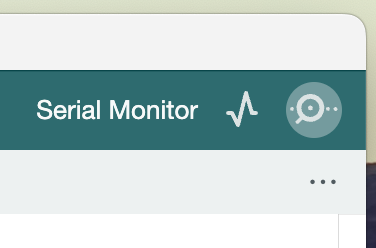
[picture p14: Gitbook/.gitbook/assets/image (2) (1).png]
<figure><figcaption></figcaption></figure>

This will present what is output on the serial port by the board, which you can use to deduce where the issues are coming from.

e.g. it can display "sensor not found on I2C bus" even when the sensor board is connected meaning that there is a connection issue between the node computer and sensor board).

{% hint style="info" %}
The serial output will only output things that it has been coded to output, so it is your responsibility to leave serial print commands in your code for debugging.
{% endhint %}

### Development

#### Node Library - to code a node

{% tabs %}
{% tab title="API reference" %}
* The `Node` class methods provide a high-level interface for interacting with a CAN bus network, abstracting away the complexities of direct hardware manipulation.
* The `VariableType` enumeration and `ExpectedMessage` structure facilitate the definition and handling of expected messages within the CAN network.

#### Usage Notes

* `uint32_t id`: The identifier of the expected message.
* `VariableType var1Type`: The type of the first variable in the message payload.
* `VariableType var2Type`: The type of the second variable in the message payload.

A structure representing an expected message with its identifier and variable types:

**`ExpectedMessage`**

* `INT32`: 32-bit signed integer.
* `UINT32`: 32-bit unsigned integer.
* `FLOAT`: Floating-point number.
* `NONE`: No variable (used when there is only one variable).

An enumeration defining the possible types of variables that can be included in a CAN message:

**`VariableType`**

12. `void initializeCANBus(gpio_num_t canRxPin, gpio_num_t canTxPin, uint8_t canStdbyPin, bool listenMode)`&#x20;
    * Initialises the CAN bus with the specified pins and mode.
13. `template <typename T> void convertToBytes(T value, byte *buffer)`&#x20;
    * Converts a value of type `T` to a byte array.

**Private Methods**

1. `void begin(gpio_num_t canRxPin = GPIO_NUM_NC, gpio_num_t canTxPin = GPIO_NUM_NC, uint8_t canStdbyPin = 0, bool listenMode = false)`
   * Initialises the CAN bus with the specified pins and mode.
2. `void initializeMessage(uint32_t id, uint8_t dataLength)`&#x20;
   * Initialises a message container with the specified ID and data length.
3. `void deleteMessage(uint32_t id)`&#x20;
   * Deletes a message from the `messages` container.
4. `template <typename T1, typename T2 = std::nullptr_t> void updateMessageData(uint32_t id, T1 var1, T2 var2 = nullptr)`&#x20;
   * Updates the data of a message with the given ID in the Node's message map.
5. `void transmitAllMessages(bool lowPowerMode = false, uint32_t sleepDurationMs = 1000)`&#x20;
   * Transmits all messages in the Node's message map to the CAN bus.
6. `void transmitMessage(uint32_t id, TickType_t ticks_to_wait = pdMS_TO_TICKS(1000))`&#x20;
   * Transmits a specific message with the specified ID and waits for the specified number of ticks.
7. `void addExpectedMessage(uint32_t id, VariableType var1Type)`&#x20;
   * Adds a single expected message with only one variable.
8. `void addExpectedMessage(uint32_t id, VariableType var1Type, VariableType var2Type)`&#x20;
   * Adds an expected message with two variables.
9. `void addExpectedMessages(const std::vector<ExpectedMessage> &messages)`&#x20;
   * Adds a collection of expected messages to the internal map.
10. `std::pair<uint32_t, std::pair<String, String>> parseReceivedMessage()`&#x20;
    * Parses the received CAN message and returns the message ID and string representations of the first and second variables in the message payload.
11. `void displayLatestMessageData()`&#x20;
    * Displays the data of the latest message in the Node's message map.

**Public Methods**

Creates an instance of the `Node` class.

```cpp
Node();
```

**Constructor**

**`Node`**

#### Classes and Structures

The `Node` library provides a framework for interacting with a CAN bus network using the ESP-IDF framework on ESP32 devices. It includes functionalities for initializing the CAN bus, sending and receiving messages, and managing message expectations.

The `Node` library provides a framework for interacting with a CAN bus network using the ESP-IDF framework on ESP32 devices. It includes functionalities for initializing the CAN bus, sending and receiving messages, and managing message expectations.

#### Classes and Structures

**`Node`**

**Constructor**

```cpp
Node();
```

Creates an instance of the `Node` class.

**Public Methods**

1. `void begin(gpio_num_t canRxPin = GPIO_NUM_NC, gpio_num_t canTxPin = GPIO_NUM_NC, uint8_t canStdbyPin = 0, bool listenMode = false)`
   * Initialises the CAN bus with the specified pins and mode.
2. `void initializeMessage(uint32_t id, uint8_t dataLength)`&#x20;
   * Initialises a message container with the specified ID and data length.
3. `void deleteMessage(uint32_t id)`&#x20;
   * Deletes a message from the `messages` container.
4. `template <typename T1, typename T2 = std::nullptr_t> void updateMessageData(uint32_t id, T1 var1, T2 var2 = nullptr)`&#x20;
   * Updates the data of a message with the given ID in the Node's message map.
5. `void transmitAllMessages(bool lowPowerMode = false, uint32_t sleepDurationMs = 1000)`&#x20;
   * Transmits all messages in the Node's message map to the CAN bus.
6. `void transmitMessage(uint32_t id, TickType_t ticks_to_wait = pdMS_TO_TICKS(1000))`&#x20;
   * Transmits a specific message with the specified ID and waits for the specified number of ticks.
7. `void addExpectedMessage(uint32_t id, VariableType var1Type)`&#x20;
   * Adds a single expected message with only one variable.
8. `void addExpectedMessage(uint32_t id, VariableType var1Type, VariableType var2Type)`&#x20;
   * Adds an expected message with two variables.
9. `void addExpectedMessages(const std::vector<ExpectedMessage> &messages)`&#x20;
   * Adds a collection of expected messages to the internal map.
10. `std::pair<uint32_t, std::pair<String, String>> parseReceivedMessage()`&#x20;
    * Parses the received CAN message and returns the message ID and string representations of the first and second variables in the message payload.
11. `void displayLatestMessageData()`&#x20;
    * Displays the data of the latest message in the Node's message map.

**Private Methods**

12. `void initializeCANBus(gpio_num_t canRxPin, gpio_num_t canTxPin, uint8_t canStdbyPin, bool listenMode)`&#x20;
    * Initialises the CAN bus with the specified pins and mode.
13. `template <typename T> void convertToBytes(T value, byte *buffer)`&#x20;
    * Converts a value of type `T` to a byte array.

**`VariableType`**

An enumeration defining the possible types of variables that can be included in a CAN message:

* `INT32`: 32-bit signed integer.
* `UINT32`: 32-bit unsigned integer.
* `FLOAT`: Floating-point number.
* `NONE`: No variable (used when there is only one variable).

**`ExpectedMessage`**

A structure representing an expected message with its identifier and variable types:

* `uint32_t id`: The identifier of the expected message.
* `VariableType var1Type`: The type of the first variable in the message payload.
* `VariableType var2Type`: The type of the second variable in the message payload.

#### Usage Notes

* The `Node` class methods provide a high-level interface for interacting with a CAN bus network, abstracting away the complexities of direct hardware manipulation.
* The `VariableType` enumeration and `ExpectedMessage` structure facilitate the definition and handling of expected messages within the CAN network.
{% endtab %}

{% tab title="Example sketch" %}
This example code initialises the CAN messages in the setup, and then in the loop updates them and sends them onto the bus.

```cpp
#include "Node.h"

/**
 * Pin Configuration for XIAO ESP32-C3 and XIAO ESP32-S3
 *
 * This section defines the GPIO pins used for TX, RX, and controlling
 * the sleep mode of the CAN transceiver chip based on the specific
 * board variant being used. Ensure that you select the correct pin
 * configuration for your hardware setup.
 *
 * TX_GPIO_NUM: Transmit Pin
 * - XIAO ESP32-C3: GPIO_NUM_3
 * - XIAO ESP32-S3 (e.g. Screen Node): GPIO_NUM_2
 *
 * RX_GPIO_NUM: Receive Pin
 * - XIAO ESP32-C3: GPIO_NUM_4
 * - XIAO ESP32-S3 (e.g. Screen Node): GPIO_NUM_3
 *
 * sleepPin: Sleep Control Pin for the CAN Transceiver
 * - XIAO ESP32-C3: 2
 * - XIAO ESP32-S3: 1
 *
 * Note:
 * - Make sure to define the correct board type before setting these pins.
 * - These configurations are critical for proper communication over the CAN bus.
 */

Node node;
void setup()
{
  // Begin serial communication at a baud rate of 115200.
  // This is necessary to print messages to the serial monitor.
  Serial.begin(115200);

  // Delay for 1 second to allow the serial monitor to initialize properly.
  // This is necessary to avoid interference with serial printing.
  delay(1000);

  // Initialize the node with the specified RX and TX pins, a standby pin, and a listen mode flag.
  // The node will use the specified pins for CAN communication.
  // The standby pin is used to control the CAN transceiver.
  // The listen mode flag determines whether the node will listen for messages on the CAN bus.
  node.begin(GPIO_NUM_4, GPIO_NUM_3, 2);

  // Initialize a message container with the specified ID and data length.
  // This function is called once per message ID that is used (i.e. to be sent or received).
  // The message container is used to store the message ID and the data associated with the message.
  node.initializeMessage(10, 8);

  // Initialize another message container with another ID and data length.
  node.initializeMessage(14, 4);

  // Display the data of the latest message in the Node's message map.
  // This function iterates through the messages in the Node's message map to find
  // the message with the highest ID, which is assumed to be the latest message.
  // It then prints the ID and data of the latest message.
  node.displayLatestMessageData();

  // Add multiple expected messages.
  // This vector contains ExpectedMessage objects that represent the expected messages received by the node.
  // Each ExpectedMessage object has an ID and two variable types.
  std::vector<ExpectedMessage> messages = {
      {20, INT32, FLOAT}, // Example of a message with two variables
      {24, UINT32, NONE}  // Example of a message with only one variable
  };

  // Add the expected messages to the Node's internal map of expected messages.
  node.addExpectedMessages(messages);
}

void loop()
{
  /*
   * In the example loop, we update and transmit messages.
   * We update message 10 with sine values of i and -i.
   * We update message 14 with the value -14.0.
   * We transmit all messages.
   * We delay for 1 second before the next iteration.
   */
  for (int i = 0; i < 314; i++)
  {
    // Update message 10 with sine values of i and -i.
    node.updateMessageData(10, (sin((float)i / 100)), (sin((float)-i / 100)));

    // Update message 14 with the value -14.0.
    node.updateMessageData(14, (float)-14);

    // Transmit all messages.
    node.transmitAllMessages(false);

    // Delay for 1 second before the next iteration.
    delay(1000);
  }
}
```
{% endtab %}

{% tab title="Example screen" %}
This example code receives CAN messages on the bus and hypothetically updates the screen accordingly.

```cpp
#include "Node.h"

/**
 * Pin Configuration for XIAO ESP32-C3 and XIAO ESP32-S3
 *
 * This section defines the GPIO pins used for TX, RX, and controlling
 * the sleep mode of the CAN transceiver chip based on the specific
 * board variant being used. Ensure that you select the correct pin
 * configuration for your hardware setup.
 *
 * TX_GPIO_NUM: Transmit Pin
 * - XIAO ESP32-C3: GPIO_NUM_3
 * - XIAO ESP32-S3 (e.g. Screen Node): GPIO_NUM_2
 *
 * RX_GPIO_NUM: Receive Pin
 * - XIAO ESP32-C3: GPIO_NUM_4
 * - XIAO ESP32-S3 (e.g. Screen Node): GPIO_NUM_3
 *
 * sleepPin: Sleep Control Pin for the CAN Transceiver
 * - XIAO ESP32-C3: 2
 * - XIAO ESP32-S3: 1
 *
 * Note:
 * - Make sure to define the correct board type before setting these pins.
 * - These configurations are critical for proper communication over the CAN bus.
 */

Node node; // Create an instance of the Node class

// The setup function is called once at startup
void setup() {
  // Initialize serial communication at a baud rate of 115200.
  Serial.begin(115200);

  // Introduce a delay of 1 second to allow for serial printing.
  // This delay is necessary to avoid issues with the serial output.
  delay(1000);

  // Initialize the CAN node with the specified pins and configuration.
  // The CAN_RX pin is GPIO_NUM_4, CAN_TX pin is GPIO_NUM_3,
  // CAN_STBY pin is 2, and CAN_LISTEN_MODE is set to false.
  // The CAN_RX and CAN_TX pins are specific to the XIAO ESP32-C3 and XIAO ESP32-S3.
  // Ensure to configure the correct pin configuration for your hardware setup.
  node.begin(GPIO_NUM_4, GPIO_NUM_3, 2, false);

  // Define multiple expected messages.
  // Each message is represented by an instance of the ExpectedMessage struct.
  // The struct contains the message ID and the variable types of the expected message payload.
  // In this example, we have two messages:
  // - Message ID: 10, Variable Type: FLOAT, FLOAT
  // - Message ID: 14, Variable Type: FLOAT, NONE (no second variable)
  std::vector<ExpectedMessage> messages = {
    { 10, FLOAT, FLOAT },
    { 14, FLOAT, NONE }
  };

  // Add the expected messages to the node.
  // This informs the node about the expected messages to receive.
  node.addExpectedMessages(messages);
}

// Main loop
void loop() {
  // Parse the received message and get the message ID, variable 1, and variable 2
  // The first element of the pair is the message ID, and the second element is a pair of strings for variable 1 and variable 2
  auto parsedMessage = node.parseReceivedMessage();

  // Check if a valid message ID was returned
  if (parsedMessage.first != 0) {
    // Get the message ID, variable 1, and variable 2
    uint32_t messageId = parsedMessage.first;  // The ID of the received message
    String var1 = parsedMessage.second.first;  // The value of the first variable in the message payload
    String var2 = parsedMessage.second.second;  // The value of the second variable in the message payload

    // Print the message ID and the values of the variables on the serial monitor
    printf("Message ID: %u\n", messageId);
    printf("Var1: %s\n", var1.c_str());
    printf("Var2: %s\n", var2.c_str());
    
    // ADD THE CODE TO UPDATE THE SCREEN HERE
  }
}
```
{% endtab %}

{% tab title="Example sensor" %}
This code was made for the voltmeter node, to show the implementation of the node library with a specific sensor (i.e. TI ADS1115 ADC chip).

```cpp
#include "Node.h"
#include <Adafruit_ADS1X15.h>

/**
 * Pin Configuration for XIAO ESP32-C3 and XIAO ESP32-S3
 *
 * This section defines the GPIO pins used for TX, RX, and controlling
 * the sleep mode of the CAN transceiver chip based on the specific
 * board variant being used. Ensure that you select the correct pin
 * configuration for your hardware setup.
 *
 * TX_GPIO_NUM: Transmit Pin
 * - XIAO ESP32-C3: GPIO_NUM_3
 * - XIAO ESP32-S3 (e.g. Screen Node): GPIO_NUM_2
 *
 * RX_GPIO_NUM: Receive Pin
 * - XIAO ESP32-C3: GPIO_NUM_4
 * - XIAO ESP32-S3 (e.g. Screen Node): GPIO_NUM_3
 *
 * sleepPin: Sleep Control Pin for the CAN Transceiver
 * - XIAO ESP32-C3: 2
 * - XIAO ESP32-S3: 1
 *
 * Note:
 * - Make sure to define the correct board type before setting these pins.
 * - These configurations are critical for proper communication over the CAN bus.
 */

Adafruit_ADS1115 ads; /* Use this for the 16-bit version */

Node node;
void setup()
{
  // Initialize serial communication
  Serial.begin(115200);

  // Delay to prevent issues with serial printing
  delay(1000);

  // Initialize the Node with specific GPIO pins and standby pin
  node.begin(GPIO_NUM_4, GPIO_NUM_3, 2);

  // Initialize messages with specific IDs and data lengths
  node.initializeMessage(10, 8);
  node.initializeMessage(11, 4);

  // The ADC input range (or gain) can be changed via the following
  // functions, but be careful never to exceed VDD +0.3V max, or to
  // exceed the upper and lower limits if you adjust the input range!
  // Setting these values incorrectly may destroy your ADC!
  //                                                                ADS1015  ADS1115
  //                                                                -------  -------
  // ads.setGain(GAIN_TWOTHIRDS);  // 2/3x gain +/- 6.144V  1 bit = 3mV      0.1875mV (default)
  // ads.setGain(GAIN_ONE);        // 1x gain   +/- 4.096V  1 bit = 2mV      0.125mV
  ads.setGain(GAIN_TWO); // 2x gain   +/- 2.048V  1 bit = 1mV      0.0625mV
  // ads.setGain(GAIN_FOUR);  // 4x gain   +/- 1.024V  1 bit = 0.5mV    0.03125mV
  //  ads.setGain(GAIN_EIGHT);      // 8x gain   +/- 0.512V  1 bit = 0.25mV   0.015625mV
  //  ads.setGain(GAIN_SIXTEEN);    // 16x gain  +/- 0.256V  1 bit = 0.125mV  0.0078125mV

  // Initialize the ADS1115 ADC
  if (!ads.begin())
  {
    Serial.println("Failed to initialize ADS.");
    while (1)
      ;
  }

  // Delay after initialization
  delay(500);

  // Set the data rate for the ADS1115 ADC
  ads.setDataRate(RATE_ADS1115_8SPS);
}

void loop()
{
  // Read ADC values for differential inputs 0-1 and 2-3
  int32_t results01 = ads.readADC_Differential_0_1();
  int32_t results23 = ads.readADC_Differential_2_3();

  // Map the ADC values to the desired range
  float mapped01 = map(results01, 5100, 32640, 500, 3200) / 1E2;
  // float mapped23 = map(results23, 5100, 32640, 500, 3200) / 1E2;
  // float mappedSOC = map((int32_t)(mapped23 * 10), 0, 327, 0, 100);

  // printf("0-1: %d  2-3: %d\n", results01, results23);
  printf("%d,%d,\n", results01, results23);
  printf("%f,\n", mapped01);

  // Update the message data
  // node.updateMessageData(10, mappedSOC, mapped23);
  // node.updateMessageData(11, mapped01);
  // node.transmitAllMessages();
  
  delay(500);
}
```
{% endtab %}
{% endtabs %}

#### Design a new sensor

The sensors come in all forms, but only one shape. They all have a standardised footprint that you can build on to make new sensors while still remaining compatible with the node computer.

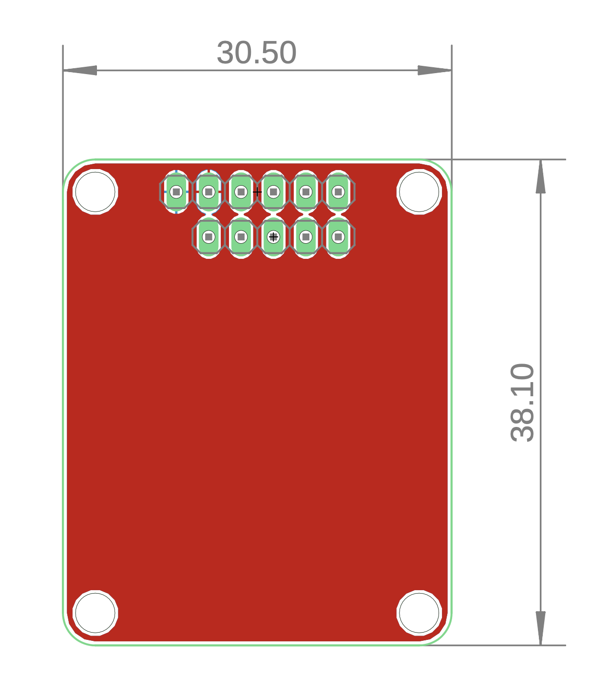
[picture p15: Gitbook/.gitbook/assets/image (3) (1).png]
<figure><figcaption><p>Template sensor shield footprint (Unit: mm)</p></figcaption></figure>

The footprint has four M3 sized holes for support, and two rows of pin headers placed just like the [node computer pinout diagram](in-the-vehicle.md#technical-specs).

The fusion PCB file can be found on the [Github repository](https://github.com/augustjaubert/UCL-SEM-Telemetry-System) under **Hardware**, and has the pin header sensor connections already pre-defined to simplify the design.

Some general help and thoughts on selecting a sensor:

* Think about what you want to know performance-wise (e.g. fuel consumption etc.), and search up what kind of sensor best suits your requirements.

You can have multiple sensors that can accomplish the same task, but have different pros and cons.&#x20;

e.g. to measure velocity, we could have had an RPM sensor or a GPS. GPS was a safer, more absolute solution, and in this case we already needed it for position.

{% hint style="info" %}
On big retailers websites (e.g. Mouser, Farnell, DigiKey, etc.) look for:

* the price (unit or bulk?),&#x20;
* availability (is it end of life?),&#x20;
* size (does it fit on the board?),&#x20;
* functionalities (handy reliability mechanisms, etc.)
{% endhint %}

* What communication protocol does it use?

Connecting to your sensor depends on the protocol the sensor uses to communicate. These can be Serial-Peripheral-Interface (SPI), Inter-Integrated Communication (I2C), UART or you have some general-purpose input/output (GPIO) pins that you can reprogram based on the ESP32-C3 or ESP32-S3 capabilities. The board also has an input for simple analog voltage reading up to 2.5V, however it is recommended to use the ADC shield instead of the ADC pins as they have lower resolution and impedance (essentially just worse, check out Espressif’s documentation).

You can see the pinout of the node computer in the [technical specifications](in-the-vehicle.md#technical-specs).

* Does it have an ECAD footprint available?

Often you are able to find the footprint ready-made by a retailer on their page (Mouser, etc.) or by a hobbyist. This simplifies the design process, however it is recommended to always double check the pinout matches that of the datasheet, as well as the dimensions.

{% hint style="info" %}
**Tip:** Find sensors with extensive online coverage (arduino tutorials, pre-existing code, etc.) as well as from breakout board manufacturers (e.g. Adafruit, Sparkfun, Seed). They often open source their electrical diagrams and code.
{% endhint %}

When it comes to wiring the sensor on the board and adding the necessary components around the chip, it is best to follow the datasheet given by the manufacturer (e.g. Texas Instruments). They often present example schematics showcasing the most common setups.

Most of the sensors developed this year were chosen because they had been covered in online tutorials, and thus had already proven code and easy-to-use libraries for them. This makes it easy to pair with our node library, as you can see in the [sensor example](in-the-vehicle.md#node-library-to-code-a-node).

#### Build a node computer

If you need to order and assemble a new node computer, you can use the gerber files provided in the [Github repository](https://github.com/augustjaubert/UCL-SEM-Telemetry-System), and upload them to JLCPCB.

{% tabs %}
{% tab title="Schematics" %}
**Electrical Diagram**

{% file src=".gitbook/assets/Node computer schematic.pdf" %}

**PCB footprint**

{% file src=".gitbook/assets/Node PCB Footprint.pdf" %}
{% endtab %}

{% tab title="3D Viewer" %}
{% embed url="https://a360.co/3WZYaDd" %}
{% endtab %}

{% tab title="Parts list (BOM)" %}
<table><thead><tr><th>Qty</th><th>Value</th><th>Device</th><th>Package</th><th width="72">Parts</th><th width="120">Description</th><th width="136">Manufacturer</th><th>Link</th><th>Unit (£)</th><th>Total (£)</th></tr></thead><tbody><tr><td>1</td><td></td><td>PINHD-1X5</td><td>1X05</td><td>JP3</td><td>PIN HEADER</td><td>n/a</td><td>n/a</td><td>n/a</td><td>#VALUE!</td></tr><tr><td>1</td><td></td><td>PINHD-1X6</td><td>1X06</td><td>JP1</td><td>PIN HEADER</td><td>n/a</td><td>n/a</td><td>n/a</td><td>#VALUE!</td></tr><tr><td>2</td><td>0</td><td>R_CHIP-0805(2012-METRIC)</td><td>RESC2012X65</td><td>R3</td><td></td><td>n/a</td><td>n/a</td><td>n/a</td><td>#VALUE!</td></tr><tr><td>3</td><td>0.1 uF</td><td>C_CHIP-0805(2012-METRIC)</td><td>CAPC2012X110</td><td>C1</td><td></td><td>n/a</td><td>n/a</td><td>n/a</td><td>#VALUE!</td></tr><tr><td>2</td><td>60</td><td>R_CHIP-0805(2012-METRIC)</td><td>RESC2012X65</td><td>R1</td><td></td><td>n/a</td><td>n/a</td><td>n/a</td><td>#VALUE!</td></tr><tr><td>1</td><td>CDSOT23-T24CAN</td><td>CDSOT23-T24CAN</td><td>SOT95P230X117-3N</td><td>D1</td><td>CAN TVS Diode</td><td>Bourns</td><td><a href="https://www.mouser.co.uk/ProductDetail/Bourns/CDSOT23-T24CAN?qs=Z7P4xsdcg2LuAOb/zQ7xoQ%3D%3D">https://www.mouser.co.uk/ProductDetail/Bourns/CDSOT23-T24CAN?qs=Z7P4xsdcg2LuAOb/zQ7xoQ%3D%3D</a></td><td>0.288</td><td>0.288</td></tr><tr><td>1</td><td>JS102011JCQN</td><td>JS102011JCQN</td><td>JS102011JCQN</td><td>S1</td><td>Slide Switches .3A 6VDC SPDT VERT MNT SMT J BEND</td><td>C &#x26; K COMPONENTS</td><td><a href="https://www.mouser.co.uk/ProductDetail/CK/JS102011JCQN?qs=74EMXstkWMWQs9mNwlyl0g%3D%3D">https://www.mouser.co.uk/ProductDetail/CK/JS102011JCQN?qs=74EMXstkWMWQs9mNwlyl0g%3D%3D</a></td><td>0.728</td><td>0.728</td></tr><tr><td>2</td><td>JST-XH-04-PIN-LONG-PAD</td><td>JST-XH-04-PIN-LONG-PAD</td><td>JST-XH-04-PACKAGE-LONG-PAD</td><td>X1</td><td></td><td>n/a</td><td>n/a</td><td>n/a</td><td>#VALUE!</td></tr><tr><td>3</td><td>NC</td><td>C_CHIP-0805(2012-METRIC)</td><td>CAPC2012X110</td><td>C3</td><td></td><td>n/a</td><td>n/a</td><td>n/a</td><td>#VALUE!</td></tr><tr><td>1</td><td>PCM12SMTR</td><td>PCM12SMTR</td><td>PCM12SMTR</td><td>S3</td><td>Slide Switches 0.3A SPDT ON-ON</td><td>C &#x26; K COMPONENTS</td><td><a href="https://www.mouser.co.uk/ProductDetail/CK/PCM12SMTR?qs=mfFuHy8STfL3qrPSfCHA7w%3D%3D&#x26;_gl=1*1yvwsae*_ga*ODY2MzE2ODU2LjE2ODk3MDQzMTM.*_ga_15W4STQT4T*MTcwODAwMTEwMS40My4wLjE3MDgwMDExMDEuNjAuMC4w*_ga_1KQLCYKRX3*MTcwODAwMTEwMS4yNy4wLjE3MDgwMDExMDEuMC4wLjA">https://www.mouser.co.uk/ProductDetail/CK/PCM12SMTR?qs=mfFuHy8STfL3qrPSfCHA7w%3D%3D&#x26;_gl=1*1yvwsae*_ga*ODY2MzE2ODU2LjE2ODk3MDQzMTM.*_ga_15W4STQT4T*MTcwODAwMTEwMS40My4wLjE3MDgwMDExMDEuNjAuMC4w*_ga_1KQLCYKRX3*MTcwODAwMTEwMS4yNy4wLjE3MDgwMDExMDEuMC4wLjA</a>.</td><td>0.8</td><td>0.8</td></tr><tr><td>1</td><td>PMEG1020EJ</td><td>PMEG1020EJ</td><td>SOD-323</td><td>D4</td><td>Schottky Rectifier, 10 V, 2 A, Single, SOD-323, 2 Pins, 460 mV</td><td>NEXPERIA</td><td><a href="https://www.mouser.co.uk/ProductDetail/Nexperia/PMEG1020EJ115?qs=LOCUfHb8d9tlKh8c7mukrA%3D%3D">https://www.mouser.co.uk/ProductDetail/Nexperia/PMEG1020EJ115?qs=LOCUfHb8d9tlKh8c7mukrA%3D%3D</a></td><td>0.24</td><td>0.24</td></tr><tr><td>1</td><td>QWIIC_RIGHT_ANGLE</td><td>QWIIC_CONNECTORJS-1MM</td><td>JST04_1MM_RA</td><td>J1</td><td>SparkFun I2C Standard Qwiic Connector</td><td>n/a</td><td>n/a</td><td>n/a</td><td>#VALUE!</td></tr><tr><td>1</td><td>TCAN1462VDRQ1</td><td>TCAN1462VDRQ1</td><td>SOIC127P600X175-8N</td><td>IC2</td><td>CAN FD transceiver</td><td>Texas Instruments</td><td><a href="https://www.mouser.co.uk/ProductDetail/Texas-Instruments/TCAN1462VDRQ1?qs=rQFj71Wb1eU28cwJFt9kYg%3D%3D">https://www.mouser.co.uk/ProductDetail/Texas-Instruments/TCAN1462VDRQ1?qs=rQFj71Wb1eU28cwJFt9kYg%3D%3D</a></td><td>1.63</td><td>1.63</td></tr><tr><td>1</td><td>XIAO-ESP32C3</td><td>XIAO-ESP32C3</td><td>XIAO-ESP32C3-MODULE14P-2.54-21X17.8MM</td><td>U1</td><td>Seeed Studio XIAO ESP32C3</td><td>Seed</td><td><a href="https://thepihut.com/products/seeed-xiao-esp32c3">https://thepihut.com/products/seeed-xiao-esp32c3</a></td><td>5</td><td>5</td></tr></tbody></table>
{% endtab %}
{% endtabs %}

Some tips on soldering the node computer,&#x20;

* Start with the bottom surface with the slide switch
* Progress to the other small components
* Place large components before placing the smaller ones around it (e.g. CAN transceiver before its capacitors)
* On the top side, place the switch first, then the MCU, then the JST sockets and finally the female pin headers. Note that the pin headers are male on the Fusion 360 project, which is not a problem since male and female have the same PCB footprint.

## Receiver

The receiver is a computer board, who’s only function is to receive those sensor messages, store them onto a microSD card and handle the radio.

The receiver hardware diagram is presented in the figure below.

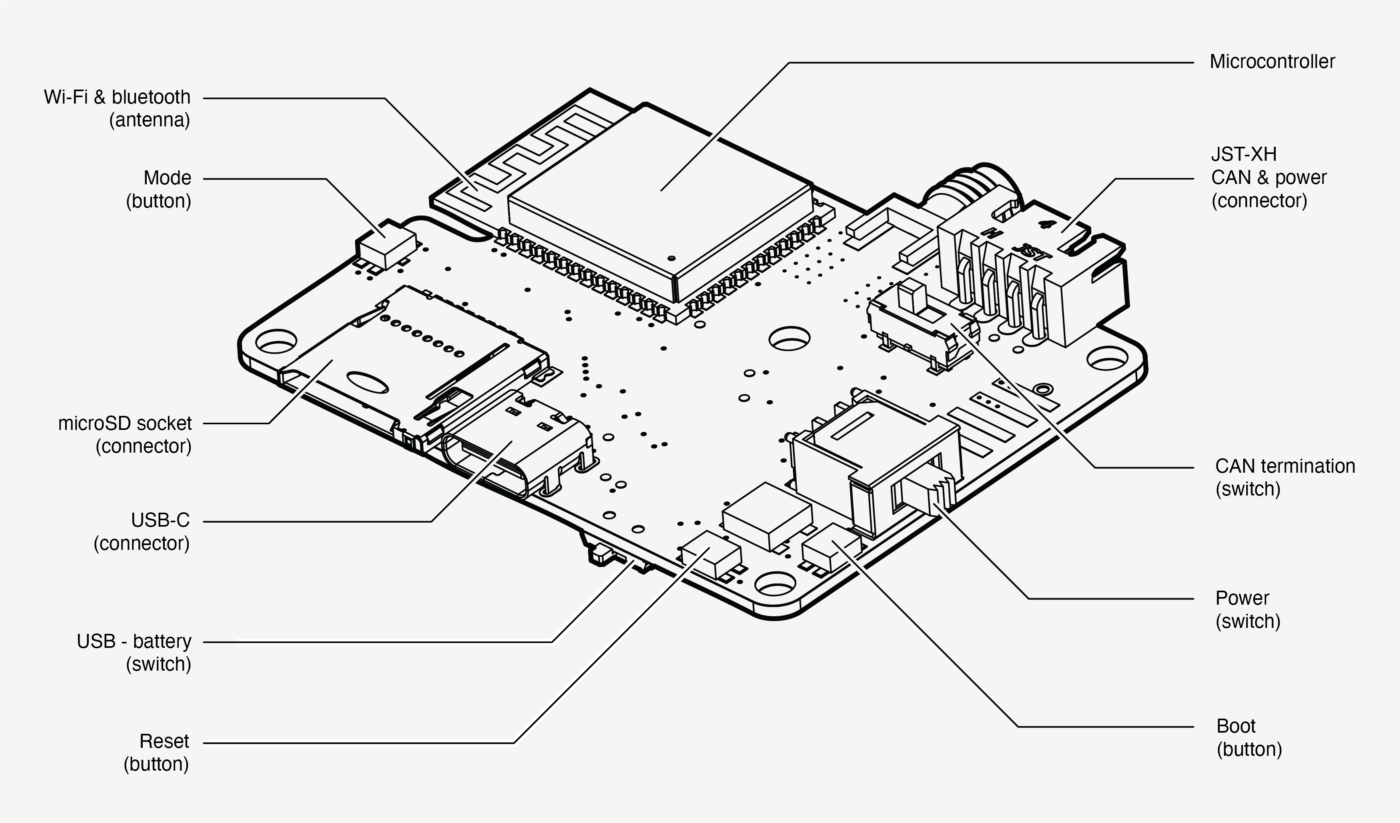
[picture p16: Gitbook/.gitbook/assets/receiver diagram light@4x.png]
<figure><picture><source srcset=".gitbook/assets/receiver diagram dark@4x.png" media="(prefers-color-scheme: dark)"></picture><figcaption><p>Technical diagram of the receiver</p></figcaption></figure>

### Technical specs

{% tabs %}
{% tab title="Tech specs" %}
The receiver uses a [ESP32-S3-WROOM-1-N16R2](https://www.espressif.com/sites/default/files/documentation/esp32-s3-wroom-1\_wroom-1u\_datasheet\_en.pdf) module as a microcontroller.

On the top surface it has,

* a microSD socket for datalogging using the ESP's native SD\_MMC library
* a USB-C port to connect to a computer
* boot and reset buttons like any Arduino board
* an Adafruit SK6812 RGB LED, programmable with [Adafruit's Neopixel Library](https://www.arduino.cc/reference/en/libraries/adafruit-neopixel/)
* a programmable mode button
* a 4 pin JST-XH connector similar to the node computers for CAN and power
* a CAN termination switch and a power switch to the rest of the system (nodes)
* a Omron XW4K-04A1-V1 board side connector socket to receive 5V from a power source (battery, etc.) connected with a Omron XW4H-04A1 wire side connector plug

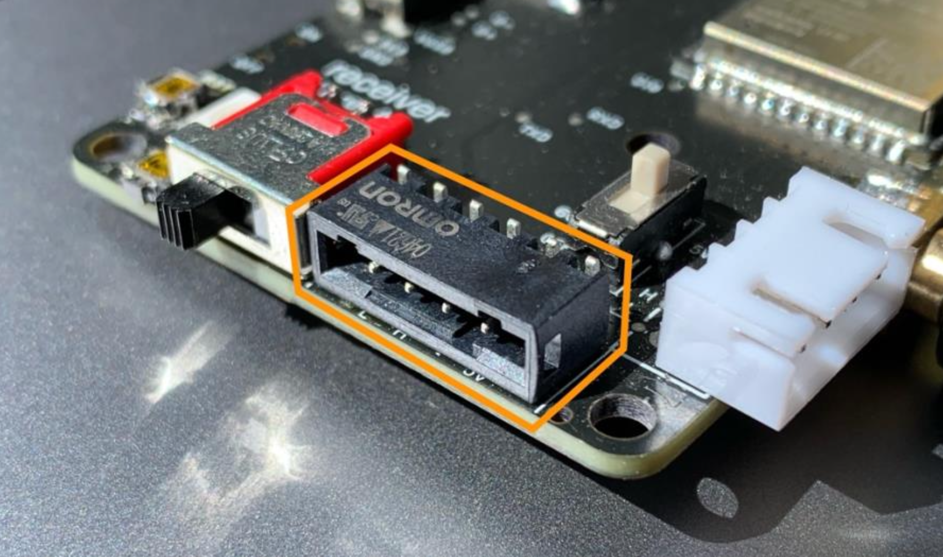
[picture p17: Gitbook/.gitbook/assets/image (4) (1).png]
<figure><figcaption><p>Image of the soldered Omron XW4K-04A1-V1 board side connector socket</p></figcaption></figure>

On the underside it has,

* a USB - Battery power switch, to disconnect the battery from the receiver MCU (hard reset)
* a 433MHz RFM69HCW radio module
* a male SMA radio antenna connector

It can be programmed and display data on the serial port by connecting to a computer through the USB-C port, and opening an IDE (Arduino IDE, PlatformIO or ESP-IDF).
{% endtab %}

{% tab title="Pinout" %}
| Pin Description |  ESP32-S3-WROOM-1-N16R2 |
| --- | --- |
| RFM69\_DIO\_0 | GPIO 3 |
| RFM69\_DIO\_1 | GPIO 9 |
| RFM69\_DIO\_2 | GPIO 10 |
| RFM69\_RESET | GPIO 48 |
| RFM69\_NSS (SPI Chip Select) | GPIO 47 |
| SPI\_SCK (RMF69) | GPIO 12 |
| SPI\_MOSI (RMF69) | GPIO 11 |
| SPI\_MISO (RFM69) | GPIO 13 |
| CAN\_TX | GPIO 18 |
| CAN\_RX | GPIO 8 |
| CAN\_STANDBY | GPIO 35 |
| MODE\_BUTTON | GPIO 14 |
| NEOPIXEL\_LED | GPIO 21 |
| SD\_DAT0 | GPIO 6 |
| SD\_DAT1 | GPIO 5 |
| SD\_DAT2 | GPIO 17 |
| SD\_DAT3 | GPIO 16 |
| SD\_CMD | GPIO 15 |
| SD\_CD | GPIO 4 |
{% endtab %}
{% endtabs %}

### Setup

#### Hardware

1. Assembling the receiver case (in ascending order)

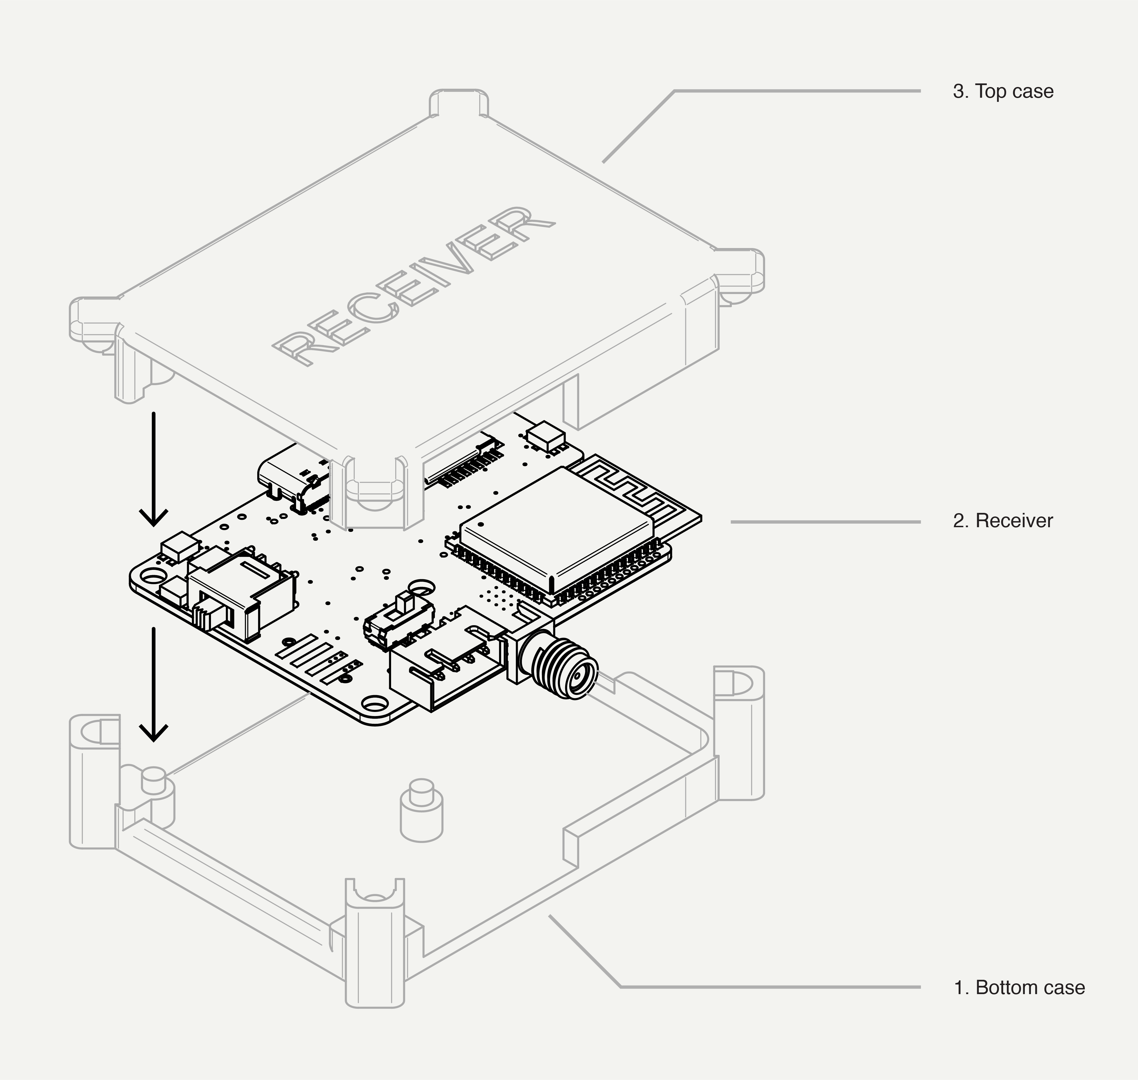
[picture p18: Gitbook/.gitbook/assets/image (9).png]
<figure><figcaption></figcaption></figure>

2. Attaching the node to the CAN/Power bus

Just like on the nodes, there is a JST-XH socket to connect the receiver to the CAN and Power bus.

The Omron socket also has CAN lines so that if a power source also has a CAN output (e.g. Battery BMS system outputting CAN messages), they can be attached to the same connector plug.&#x20;

You can see the connection placement in the centre of the image below, where **L is for CAN\_LOW**, **H for CAN\_HIGH**, **- for GROUND** and **5V for +5V**.

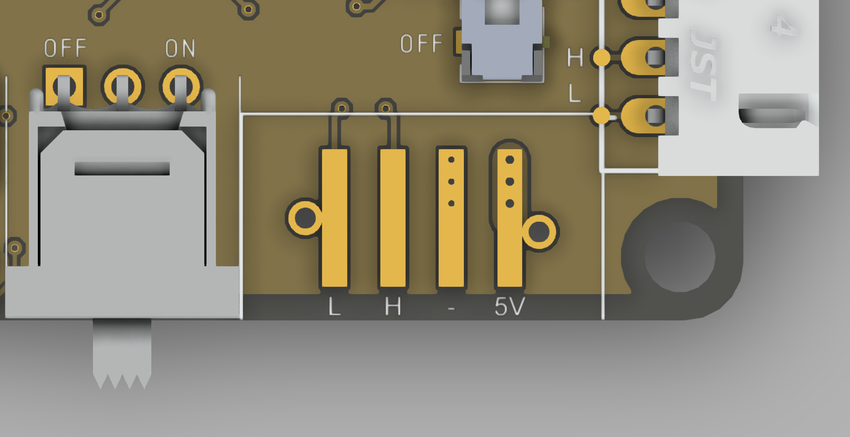
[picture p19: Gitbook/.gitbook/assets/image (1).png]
<figure><figcaption></figcaption></figure>

3. Installing in the vehicle

Just like for [a node](in-the-vehicle.md#hardware), you can then place the receiver anywhere in the vehicle.

#### Software

Similar to in the [node software setup](in-the-vehicle.md#software).

<details>

<summary>Similar steps</summary>

1. Installing the integrated development environment (IDE)

The system works similar to most Arduino projects, as it has been coded in C++ using the Arduino IDE.

Any IDE will do the job, however we recommend using the following:

[Arduino IDE](https://www.arduino.cc/en/software) <mark style="color:orange;">is the easiest to use, has plenty of documentation and forum help and is sufficient almost 99% of the time.</mark>

[Platform IO](https://platformio.org/) (through VSCode) is essentially a pro version, where you have more control but requires a manual setup.

[ESP-IDF](https://docs.espressif.com/projects/esp-idf/en/stable/esp32/get-started/index.html#introduction) is the MCU's native IDE, which gives more liberty in using all its functions.

2. ESP board definitions

The ESP boards (MCU) are not defined by default in the Arduino IDE. You will have to add them initially to be able to connect to the nodes and others.

To do this in the Arduino IDE, navigate to **File > Preferences**, and fill **"Additional Boards Manager URLs"** with the url below: [_https://raw.githubusercontent.com/espressif/arduino-esp32/gh-pages/package\_esp32\_index.json_](https://raw.githubusercontent.com/espressif/arduino-esp32/gh-pages/package\_esp32\_index.json)

Navigate to **Tools > Board > Boards Manager...**, type the keyword "**esp32**" in the search box, select the latest version of **esp32**, and install it.

</details>

3. Installing the receiver library

Download the 15 files from the [Github repository](https://github.com/augustjaubert/UCL-SEM-Telemetry-System) in the Receiver folder.

To add the receiver library to your arduino sketch[^2], add all the files in your sketch folder.

<details>

<summary>Example project organisation</summary>

<pre><code>example_sketch (folder)
-> Receiver.cpp
-> Receiver.h
-> Config.h
-> SDCardHandler.cpp
-> SDCardHandler.h
<strong>-> RadioHandler.cpp
</strong>-> RadioHandler.h
-> ModeConfig.cpp
-> ModeConfig.h
-> DataProcessing.cpp
-> DataProcessing.h
-> ConfigFileParser.cpp
-> ConfigFileParser.h
-> CANMessageParser.cpp
-> CANMessageParser.h
-> example_sketch.ino (arduino sketch)
</code></pre>

</details>

4. Connecting to the receiver board

To connect the receiver board to the arduino sketch, select the top-left text box **Select Board** and select **ESP32-S3-USB-OTG**.

<figure><figcaption></figcaption></figure>

1. Assemble the receiver (board and case).
2. Connect a CAN cable to the JST sockets to add the receiver to the CAN bus.
3. Usually the receiver is added at the end of the bus, therefore switch the CAN termination ON<mark style="color:orange;">.</mark>
   1. If the power source connector (Omron) also has a CAN input, then switch the CAN termination OFF. There will need to be a CAN termination at the power source side of the CAN bus.

### How to use

#### Steps

1. Insert the micro-SD card in the socket. See [here](in-the-vehicle.md#development-1) for more info on the telemetry data configuration.
2. Assemble the node (sensor, computer and case).
3. Connect a CAN cable to one of the JST sockets to add the node on the CAN bus.
4. If the node is added at the end of the bus, switch the CAN termination ON.

#### **Troubleshooting**

If it seems as though the receiver is not working as intended:

1. Disassemble the receiver.
2. Connect the receiver board to your laptop through USB.
3. Open Arduino IDE, and check that you have the correct board definition in the top-left text box **Select Board**.

<details>

<summary>No board appearing</summary>

If you don't see a board appearing, then the MCU is not powered, or the serial connection has been severed. This can be because,

* The USB cable is not properly connected either to the node or laptop
* The MCU is not receiving power, which can be checked with a multimeter on the MCU 3.3V pins to see if it detects a voltage. This can be due to a severed power connection on the circuit. It is recommended to check the Espressif's chip datasheet in detail.
* The serial connection is severed, which can be because&#x20;
  * the USB connector on the MCU has been damaged,&#x20;
  * or because something (e.g. static electricity) has caused your laptop to disconnect the USB port (safety mode). It happens that connection is re-established after some time.
    * You can first try to reset the board by clicking the **RESET BUTTON** once while the board is connected to your PC. If that does not work, hold the **BOOT BUTTON**, connect the board to your PC while holding the **BOOT** button, and then release it to enter **bootloader mode**.
  * a very unlucky reason can be that the MCU chip has failed. This has happened a few times in the past, and can be fixed by carefully desoldering the MCU chip with a hot air gun and heat-resistant Capton tape around other components, to then either replacing with a new chip or de-bricking the "dead" chip by connecting it with a test board module (possibly left in the MechSpace Workshop C drawers).

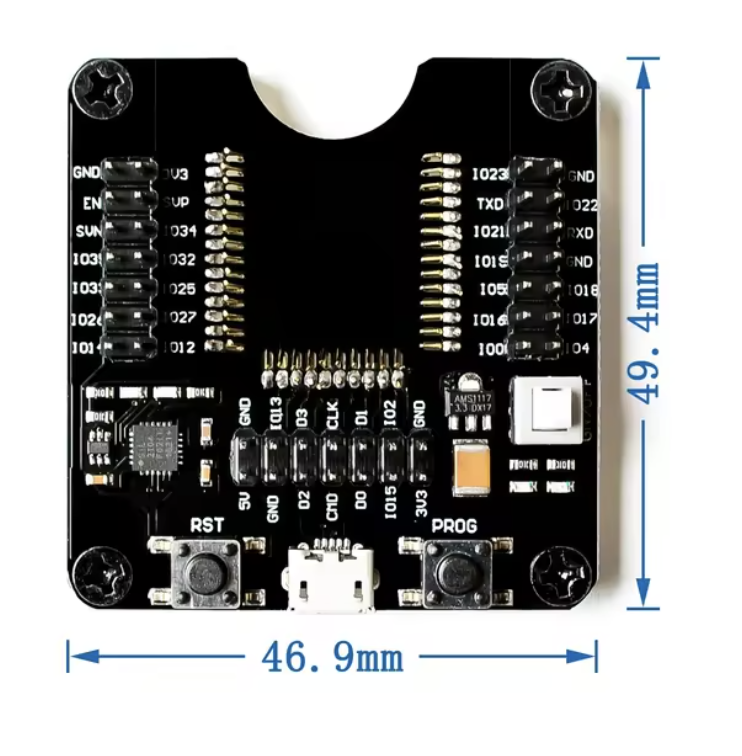
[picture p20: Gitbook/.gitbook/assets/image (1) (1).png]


</details>

<details>

<summary>The wrong board is appearing</summary>

If the wrong board is appearing, that is a good sign because it recognises something.

You can open the text box, click on select **other board and port...** and search for the appropriate board (ESP32-S3-USB-OTG).

</details>

4. Open the serial monitor, in the top-right corner.

<figure><figcaption></figcaption></figure>

This will present what is output on the serial port by the board, which you can use to deduce where the issues are coming from.

{% hint style="info" %}
The serial output will only output things that it has been coded to output, so it is your responsibility to leave serial print commands in your code for debugging.

This also means that you can check the receiver sketch and library codebase to find out where from the serial print output is coming from in the code.
{% endhint %}

### Development

#### Receiver Library

{% hint style="info" %}
The Receiver codebase is quite a convoluted assortment of libraries to separate and classify all the different functions.&#x20;

There is a handler for everything SD communication related, Radio related, mode button,&#x20;
{% endhint %}

{% tabs %}
{% tab title="API Reference" %}
The `Receiver` library provides a framework for interacting with a CAN bus network using the ESP-IDF framework on ESP32 devices. It includes functionalities for initialising an SD card, a CAN bus, receiving, processing and storing CAN messages, and transmitting them over radio.

#### Classes and Structures

**`Receiver`**

**Constructor**

```cpp
Receiver::Receiver(const String& configFilePath)
```

Creates a new `Receiver` instance initialized with the specified configuration file path.

**Public Methods**

1. `void Receiver::begin(bool liveSendingMode)`
   * Initialises the Receiver object by setting up the SD card, radio, configuration parser, and CAN interface. liveSendingMode Flag indicating whether to enable live sending mode.
2. `void Receiver::receiveCAN(SemaphoreHandle_t& dataMutex, bool displayParameters)`&#x20;
   * Receives a CAN message and handles it if the message is valid.
     * dataMutex is a semaphore handle used to protect access to shared data.
     * the displayParameters Flag indicating whether to display updated parameters after handling the message.
3. `void Receiver::printParameters()`&#x20;
   * Prints the CAN message parameters stored in the configuration parser.
4. `void Receiver::displayUpdatedParameters()`&#x20;
   * Displays the updated parameters by iterating over the CAN message configurations and checking for updates.
5. `void transmitAllMessages(bool lowPowerMode = false, uint32_t sleepDurationMs = 1000)`&#x20;
   * Transmits all messages in the Node's message map to the CAN bus.
6. `void Receiver::initLapFence(float latA, float lngA, float latB, float lngB, float latC, float lngC, float latD, float lngD)`
   * Initialises the lap fence to count laps with the given coordinates.
7. `void Receiver::initRadioFence(float latA, float lngA, float latB, float lngB, float latC, float lngC, float latD, float lngD)`
   * Initialises the radio fence to send telemetry data with the given coordinates.
8. `void Receiver::togglePrintStatements()`
   * Toggles the state of print statements.

#### Usage Notes

* The `Receiver` class provides a high-level interface for handling CAN messages, radio communication, and SD card operations in a receiver system. It abstracts away the complexities of direct hardware manipulation, making it easier to integrate these functionalities into a larger system.
* Key features include:
  * Initialisation of the receiver system with configurable options
  * Reception and handling of CAN messages
  * Displaying and updating of CAN message parameters
  * Support for both lap fences and radio fences
  * Toggleable print statements for debugging and monitoring
  *
{% endtab %}

{% tab title="Example sketch" %}
This example shows the use of the receiver library in the receiver sketch.

```cpp
#include <RHReliableDatagram.h>
#include <Adafruit_NeoPixel.h>
#include "freertos/FreeRTOS.h"
#include "freertos/task.h"
#include "driver/twai.h"
#include "esp_system.h"
#include <RH_RF69.h>
#include "esp_err.h"
#include "esp_log.h"
#include <stdlib.h>
#include "SD_MMC.h"
#include <stdio.h>
#include <SPI.h>
#include "FS.h"
#include <map>
#include <EEPROM.h>

#include "Receiver.h"

#define ESP_EXCEPTION_DECODER

Receiver receiver("/config/README.txt");

SemaphoreHandle_t dataMutex;  // Mutex to protect shared data

void CANHandlerTask(void *pvParameters) {
  for (;;) {
    // Handle button press events here
    receiver.receiveCAN(dataMutex, true);
    //receiver.displayUpdatedParameters();
    vTaskDelay(pdMS_TO_TICKS(0));  // Adjust delay according to your application requirements
  }
}

void setup() {
  Serial.begin(115200);

  delay(100);  // delay to let serial begin have a breather huff huff

  receiver.begin(true);
  receiver.printParameters();

  //receiver.initLapFence(51.5280372, -0.1426583, 51.5280462, -0.1425165, 51.5279792, -0.1425112, 51.5279757, -0.1426627);    // NW1 3QS Compton Close Park
  //receiver.initRadioFence(51.5280363, -0.1430492, 51.5280545, -0.1422529, 51.5279662, -0.1422228, 51.5279683, -0.1430449);  // NW1 3QS Compton Close Park

  //receiver.initLapFence(51.4199761, 0.3482651, 51.4200143, 0.3483264, 51.4198693, 0.3488128, 51.4198191, 0.3487607);    // CycloPark
  //receiver.initRadioFence(51.4205795, 0.3484007, 51.4206552, 0.3484280, 51.4202241, 0.3496966, 51.4201799, 0.3496453);  // CycloPark

  receiver.initLapFence(43.7708310, -0.0408539, 43.7709265, -0.0406479, 43.7706997, -0.0404429, 43.7706075, -0.0406456);    // Nogaro track
  receiver.initRadioFence(43.7719449, -0.0423221, 43.7723014, -0.0417674, 43.7712505, -0.0403314, 43.7707955, -0.0409531);  // Nogaro track

  // Create mutex
  dataMutex = xSemaphoreCreateMutex();
  if (dataMutex == NULL) {
    printf("Failed to create mutex\n");
    // Handle the error appropriately, e.g., stop the program
    while (1)
      ;
  }

  xTaskCreatePinnedToCore(
    CANHandlerTask,    // Task function
    "CANHandlerTask",  // Task name
    4096,              // Stack size (bytes)
    NULL,              // Task parameters
    3,                 // Task priority
    NULL,              // Task handle
    0                  // Core to run the task (0 or 1)
  );
}

void loop() {
}
```
{% endtab %}
{% endtabs %}

#### Telemetry Data Configuration

On the SD card connected to the receiver there is a **config** folder with a **README.TXT** file.

The README file is used to configure the telemetry messages received from nodes and which ones to be sent over radio to the race engineer.

<details>

<summary>README file format</summary>

The format of the configuration is,

```
<Message_name>, <CAN_ID>, <Param1_Name>, <Param1_Unit>, <Param1_type>, <Param1_bits>, <Param2_Name>, <Param2_Unit>,<Param2_type>,<Param2_bits>
```

For example, for the GPS node which we will name GPS1,

* a CAN bus message ID of 10&#x20;
* sending latitude in degrees in the first 4 bytes with a variable type of 32-bit integer
* sending longitude in degrees in the last 4 bytes with a variable type of 32-bit integer

Altogether, to add a message from the GPS node into one line,

```
GPS1, 22, Lat, deg, I, 32, Lon, deg, I, 32
```

To specify wether the message is also to be forwarded to the race engineer over radio, you can add an @ sign in front of the line.

<pre><code><strong>@GPS1, 22, Lat, deg, I, 32, Lon, deg, I, 32
</strong></code></pre>

This process is repeated for all the expected messages from the nodes,

```
<Message_name>, <CAN_ID>, <Param1_Name>, <Param1_Unit>, <Param1_type>, <Param1_bits>, <Param2_Name>, <Param2_Unit>,<Param2_type>,<Param2_bits>

@SUPCAP1, 10, SOC,%, F, 32, CAP_Volt, V,F, 32

THROTTLE, 11, Volt1_2, V,F,32

@CURR1, 14, Curr1, A,F, 32, Curr1_raw, bit, I, 32

@CURR2, 15, Curr2, A, F, 32, Curr2_raw, bit, I, 32

@CURR3, 16, Curr3, A,F, 32, Curr3_raw, bit, I, 32

GPS1, 22, Lat, deg, I, 32, Lon, deg, I, 32

etc...
```

When the receiver sees a message and cross-identifies it from the README file, it will record it into a folder with its Message\_name. Messages that are not written down correctly onto the README file will not be recorded onto the SD card.

</details>

<details>

<summary>How radio modes work</summary>

There are two radio modes:

* **Live-send telemetry**, where all the data to be sent is sent the instant it is received by the in-vehicle receiver and is never sent again after that. This is useful to have real-time information, but is only possible if the vehicle is in view and at a short distance (e.g. 200m)
* **Batch-send telemetry**, where all the data to be sent is stored in a file on the SD card until the vehicle enters a pre-defined geofenced zone where it starts sending all the stored data for a lap together. The idea is that you would be sending a whole lap's data just in one section of the track. This is useful if the vehicle is not in view at all times, or if it goes further than the max transmission distance (400-500m).

To activate either mode, you need to define it in the begin statement of the Receiver class/object.

```cpp
Receiver receiver("/config/README.txt");
bool liveSendModeOn = false; // This means the batch-send mode will be used
...
void setup() {
  receiver.begin(liveSendModeOn);
...
}
```

</details>

#### Build a receiver

If you need to order and assemble a new receiver, you can use the gerber files provided in the [Github repository](https://github.com/augustjaubert/UCL-SEM-Telemetry-System), and upload them to JLCPCB.

{% tabs %}
{% tab title="Schematics" %}
**Electrical Diagram**

{% file src=".gitbook/assets/receiver v2ra schematic.pdf" %}

**PCB footprint**

{% file src=".gitbook/assets/Receiver PCB Footprint.pdf" %}
{% endtab %}

{% tab title="3D Viewer" %}
{% embed url="https://a360.co/3wpQ9fS" %}
{% endtab %}

{% tab title="Parts list (BOM)" %}
<table><thead><tr><th>Qty</th><th>Value</th><th>Device</th><th>Package</th><th>Parts</th><th>Description</th><th>MANUFACTURER_NAME</th><th>MANUFACTURER_PART_NUMBER</th><th width="94">Link</th><th>Unit (£)</th><th>Total (£)</th></tr></thead><tbody><tr><td>1</td><td></td><td>SMA CONNECTOR EDGE</td><td>SMA_EDGELAUNCH</td><td>X1</td><td>SMA Female Connector</td><td>Amazon</td><td>N/A</td><td><a href="https://www.amazon.co.uk/100PCS-Female-Coaxial-Connector-Material/dp/B0B2KTBDZX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;keywords=kerlife+10Pcs+Brass+SMA+Female+PCB+Panel+Mount+Connector+Female+Base+Socket+Jack+50+Ohm+RF+Connectors+for+Wireless+Device+Equipments&#x26;qid=1708338485&#x26;sprefix=kerlife+10pcs+brass+sma+female+pcb+panel+mount+connector+female+base+socket+jack+50+ohm+rf+connectors+for+wireless+device+equipments,aps,64&#x26;sr=8-1">https://www.amazon.co.uk/100PCS-Female-Coaxial-Connector-Material/dp/B0B2KTBDZX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;keywords=kerlife+10Pcs+Brass+SMA+Female+PCB+Panel+Mount+Connector+Female+Base+Socket+Jack+50+Ohm+RF+Connectors+for+Wireless+Device+Equipments&#x26;qid=1708338485&#x26;sprefix=kerlife+10pcs+brass+sma+female+pcb+panel+mount+connector+female+base+socket+jack+50+ohm+rf+connectors+for+wireless+device+equipments,aps,64&#x26;sr=8-1</a></td><td>0.1953</td><td>0.1953</td></tr><tr><td>1</td><td>0</td><td>R_CHIP-0603(1608-METRIC)</td><td>RESC1608X60</td><td>R22</td><td>Resistor Fixed - SMD</td><td></td><td></td><td></td><td></td><td>0</td></tr><tr><td>2</td><td>0.1 uF</td><td>C_CHIP-0603(1608-METRIC)</td><td>CAPC1608X85</td><td>C1</td><td>Capacitor - Ceramic SMD</td><td></td><td></td><td></td><td></td><td>0</td></tr><tr><td>7</td><td>0.1uF</td><td>C_CHIP-0603(1608-METRIC)</td><td>CAPC1608X85</td><td>C2</td><td>Capacitor - Ceramic SMD</td><td></td><td></td><td></td><td></td><td>0</td></tr><tr><td>2</td><td>0.1uF (NC)</td><td>C_CHIP-0603(1608-METRIC)</td><td>CAPC1608X85</td><td>C12</td><td>Capacitor - Ceramic SMD</td><td></td><td></td><td></td><td></td><td>0</td></tr><tr><td>2</td><td>100k</td><td>R_CHIP-0603(1608-METRIC)</td><td>RESC1608X60</td><td>R2</td><td>Resistor Fixed - SMD</td><td></td><td></td><td></td><td></td><td>0</td></tr><tr><td>12</td><td>10k</td><td>R_CHIP-0603(1608-METRIC)</td><td>RESC1608X60</td><td>R4</td><td>Resistor Fixed - SMD</td><td></td><td></td><td></td><td></td><td>0</td></tr><tr><td>4</td><td>10uF</td><td>C_CHIP-0805(2012-METRIC)</td><td>CAPC2012X110</td><td>C5</td><td>Capacitor - Ceramic SMD</td><td></td><td></td><td></td><td></td><td>0</td></tr><tr><td>1</td><td>1k</td><td>R_CHIP-0603(1608-METRIC)</td><td>RESC1608X60</td><td>R25</td><td>Resistor Fixed - Generic</td><td></td><td></td><td></td><td></td><td>0</td></tr><tr><td>1</td><td>1uF</td><td>C_CHIP-0603(1608-METRIC)</td><td>CAPC1608X85</td><td>C20</td><td>Capacitor - Ceramic SMD</td><td></td><td></td><td></td><td></td><td>0</td></tr><tr><td>1</td><td>300</td><td>R_CHIP-0603(1608-METRIC)</td><td>RESC1608X60</td><td>R12</td><td>Resistor Fixed - Generic</td><td></td><td></td><td></td><td></td><td>0</td></tr><tr><td>1</td><td>400k</td><td>R_CHIP-0603(1608-METRIC)</td><td>RESC1608X60</td><td>R21</td><td>Resistor Fixed - Generic</td><td></td><td></td><td></td><td></td><td>0</td></tr><tr><td>2</td><td>5.1k</td><td>R_CHIP-0603(1608-METRIC)</td><td>RESC1608X60</td><td>R3</td><td>Resistor Fixed - SMD</td><td></td><td></td><td></td><td></td><td>0</td></tr><tr><td>1</td><td>500</td><td>R_CHIP-0603(1608-METRIC)</td><td>RESC1608X60</td><td>R1</td><td>Resistor Fixed - SMD</td><td></td><td></td><td></td><td></td><td>0</td></tr><tr><td>2</td><td>60</td><td>R_CHIP-0805(2012-METRIC)</td><td>RESC2012X65</td><td>R8_C</td><td>Resistor Fixed - SMD</td><td></td><td></td><td></td><td></td><td>0</td></tr><tr><td>4</td><td>NC</td><td>C_CHIP-0603(1608-METRIC)</td><td>CAPC1608X85</td><td>C4</td><td>Capacitor - Ceramic SMD</td><td></td><td></td><td></td><td></td><td>0</td></tr><tr><td>2</td><td>NC</td><td>R_CHIP-0603(1608-METRIC)</td><td>RESC1608X60</td><td>R14</td><td>Resistor Fixed - SMD</td><td></td><td></td><td></td><td></td><td>0</td></tr><tr><td>1</td><td>500ASSP1M6QE</td><td>500ASSP1M6QE</td><td>500ASSP1M6QE</td><td>S1</td><td>Power Slide Switch</td><td>E-SWITCH</td><td>500ASSP1M6QE</td><td><a href="https://www.mouser.co.uk/ProductDetail/E-Switch/500ASSP1M6QE?qs=%252BZnE/xbLNR9QgzPkMZRAQg%3D%3D">https://www.mouser.co.uk/ProductDetail/E-Switch/500ASSP1M6QE?qs=%252BZnE/xbLNR9QgzPkMZRAQg%3D%3D</a></td><td>3.37</td><td>3.37</td></tr><tr><td>1</td><td>CDSOT23-T24CAN</td><td>CDSOT23-T24CAN</td><td>SOT95P230X117-3N</td><td>D1</td><td>CAN TVS Diode</td><td>Bourns</td><td>CDSOT23-T24CAN</td><td><a href="https://www.mouser.co.uk/ProductDetail/Bourns/CDSOT23-T24CAN?qs=Z7P4xsdcg2LuAOb/zQ7xoQ%3D%3D">https://www.mouser.co.uk/ProductDetail/Bourns/CDSOT23-T24CAN?qs=Z7P4xsdcg2LuAOb/zQ7xoQ%3D%3D</a></td><td>0.288</td><td>0.288</td></tr><tr><td>1</td><td>COM-13909</td><td>COM-13909</td><td>MOD_COM-13909</td><td>RFM69</td><td>Rfm69hcw General ISM &#x3C; 1GHz Transceiver Module 915/433MHz Surface Mount</td><td>HOPERF</td><td>RFM69HCW</td><td><a href="https://www.mouser.co.uk/ProductDetail/Adafruit/5693?qs=mELouGlnn3fnO8nGmYJgWQ%3D%3D">https://www.mouser.co.uk/ProductDetail/Adafruit/5693?qs=mELouGlnn3fnO8nGmYJgWQ%3D%3D</a></td><td>4.76</td><td>4.76</td></tr><tr><td>1</td><td>ESP32-S3-WROOM-1-N16R2</td><td>ESP32-S3-WROOM-1-N16R2</td><td>XCVR_ESP32-S3-WROOM-1-N16R2</td><td>U1</td><td>Espressif ESP32-S3 Microcontroller</td><td>Espressif</td><td>ESP32-S3-WROOM-1-N16R2</td><td><a href="https://www.amazon.co.uk/gp/product/B09TPMJ8SN/ref=ox_sc_saved_title_1?smid=A30DC7701CXIBH&#x26;psc=1">https://www.amazon.co.uk/gp/product/B09TPMJ8SN/ref=ox_sc_saved_title_1?smid=A30DC7701CXIBH&#x26;psc=1</a></td><td>1.856</td><td>1.856</td></tr><tr><td>1</td><td>JS102011JCQN</td><td>JS102011JCQN</td><td>JS102011JCQN</td><td>S3</td><td>Slide Switch .3A 6VDC SPDT VERT MNT SMT J BEND (CAN Termination)</td><td>C &#x26; K COMPONENTS</td><td>JS102011JCQN</td><td><a href="https://www.mouser.co.uk/ProductDetail/CK/JS102011JCQN?qs=74EMXstkWMWQs9mNwlyl0g%3D%3D">https://www.mouser.co.uk/ProductDetail/CK/JS102011JCQN?qs=74EMXstkWMWQs9mNwlyl0g%3D%3D</a></td><td>0.728</td><td>0.728</td></tr><tr><td>1</td><td>JST-XH-04-PIN-LONG-PAD</td><td>JST-XH-04-PIN-LONG-PAD</td><td>JST-XH-04-PACKAGE-LONG-PAD</td><td>X4</td><td>JST XH Connector 4 Pin</td><td>Amazon</td><td>N/A</td><td><a href="https://www.amazon.co.uk/sourcing-map-Connector-Housing-Adapter/dp/B0BTGWYK4Y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;keywords=sourcing+map+2.54mm+Pitch+XH+Connector+Kits+4+Pin+Male+Female+Header+Right+Angle+Socket+Housing+Cable+Adapter+and+Crimp+DIP+Kits,+50+Set(300pcs)&#x26;qid=1708336662&#x26;sprefix=sourcing+map+2.54mm+pitch+xh+connector+kits+4+pin+male+female+header+right+angle+socket+housing+cable+adapter+and+crimp+dip+kits+50+set+300pcs+,aps,121&#x26;sr=8-1&#x26;th=1">https://www.amazon.co.uk/sourcing-map-Connector-Housing-Adapter/dp/B0BTGWYK4Y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;keywords=sourcing+map+2.54mm+Pitch+XH+Connector+Kits+4+Pin+Male+Female+Header+Right+Angle+Socket+Housing+Cable+Adapter+and+Crimp+DIP+Kits,+50+Set(300pcs)&#x26;qid=1708336662&#x26;sprefix=sourcing+map+2.54mm+pitch+xh+connector+kits+4+pin+male+female+header+right+angle+socket+housing+cable+adapter+and+crimp+dip+kits+50+set+300pcs+,aps,121&#x26;sr=8-1&#x26;th=1</a></td><td>0.02496667</td><td>0.02496667</td></tr><tr><td>1</td><td>LM1117MPX-3.3_NOPB</td><td>LM1117MPX-3.3_NOPB</td><td>SOT230P700X180-4N</td><td>IC3</td><td>Space saving 800-mA low-dropout linear regulator with internal current limit</td><td>Texas Instruments</td><td>LM1117MPX-3.3/NOPB</td><td><a href="https://www.mouser.co.uk/ProductDetail/Texas-Instruments/LM1117MPX-3.3-NOPB?qs=X1J7HmVL2ZHRbBIxXi4utg%3D%3D">https://www.mouser.co.uk/ProductDetail/Texas-Instruments/LM1117MPX-3.3-NOPB?qs=X1J7HmVL2ZHRbBIxXi4utg%3D%3D</a></td><td>0.886</td><td>0.886</td></tr><tr><td>1</td><td>MEM2075-00-140-01-A</td><td>MEM2075-00-140-01-A</td><td>MEM20750014001A</td><td>J1</td><td>MEM2075-00-140-01-A - MICRO SD CARD CONN</td><td>GCT</td><td>MEM2075-00-140-01-A</td><td><a href="https://www.mouser.co.uk/ProductDetail/GCT/MEM2075-00-140-01-A?qs=KUoIvG/9IlZvfWpeERlq3Q%3D%3D">https://www.mouser.co.uk/ProductDetail/GCT/MEM2075-00-140-01-A?qs=KUoIvG/9IlZvfWpeERlq3Q%3D%3D</a></td><td>1.58</td><td>1.58</td></tr><tr><td>1</td><td>NEOPIXEL</td><td>1655</td><td>1655</td><td>LED1</td><td>NeoPixel 5050 RGB LED with Integrated Driver Chip</td><td>Adafruit</td><td>NeoPixel 5050 - 1655</td><td><a href="https://www.mouser.co.uk/ProductDetail/Adafruit/1655?qs=GURawfaeGuATdkjqVQs49g%3D%3D">https://www.mouser.co.uk/ProductDetail/Adafruit/1655?qs=GURawfaeGuATdkjqVQs49g%3D%3D</a></td><td>0.36</td><td>0.36</td></tr><tr><td>1</td><td>PCM12SMTR</td><td>PCM12SMTR</td><td>PCM12SMTR</td><td>S2</td><td>Slide Switches 0.3A SPDT ON-ON (USB Switch)</td><td>C &#x26; K COMPONENTS</td><td>PCM12SMTR</td><td><a href="https://www.mouser.co.uk/ProductDetail/CK/PCM12SMTR?qs=mfFuHy8STfL3qrPSfCHA7w%3D%3D&#x26;_gl=1*1yvwsae*_ga*ODY2MzE2ODU2LjE2ODk3MDQzMTM.*_ga_15W4STQT4T*MTcwODAwMTEwMS40My4wLjE3MDgwMDExMDEuNjAuMC4w*_ga_1KQLCYKRX3*MTcwODAwMTEwMS4yNy4wLjE3MDgwMDExMDEuMC4wLjA">https://www.mouser.co.uk/ProductDetail/CK/PCM12SMTR?qs=mfFuHy8STfL3qrPSfCHA7w%3D%3D&#x26;_gl=1*1yvwsae*_ga*ODY2MzE2ODU2LjE2ODk3MDQzMTM.*_ga_15W4STQT4T*MTcwODAwMTEwMS40My4wLjE3MDgwMDExMDEuNjAuMC4w*_ga_1KQLCYKRX3*MTcwODAwMTEwMS4yNy4wLjE3MDgwMDExMDEuMC4wLjA</a>.</td><td>0.8</td><td>0.8</td></tr><tr><td>1</td><td>PMEG1020EJ</td><td>PMEG1020EJ</td><td>SOD-323</td><td>D4</td><td>Schottky Rectifier, 10 V, 2 A, Single, SOD-323, 2 Pins, 460 mV</td><td>NEXPERIA</td><td></td><td><a href="https://www.mouser.co.uk/ProductDetail/Nexperia/PMEG1020EJ115?qs=LOCUfHb8d9tlKh8c7mukrA%3D%3D">https://www.mouser.co.uk/ProductDetail/Nexperia/PMEG1020EJ115?qs=LOCUfHb8d9tlKh8c7mukrA%3D%3D</a></td><td>0.24</td><td>0.24</td></tr><tr><td>3</td><td>PTS841ESDGKPSMTRLFS</td><td>PTS841ESDGKPSMTRLFS</td><td>PTS841ESDGKPSMTRLFS</td><td>BOOT</td><td>Side-actuated tactile switch</td><td>C&#x26;K</td><td>PTS841 ESD GKP SMTR LFS</td><td><a href="https://www.mouser.co.uk/ProductDetail/CK/PTS841-ESD-GKP-SMTR-LFS?qs=d0WKAl%252BL4KbeUlwuiSQZWA%3D%3D">https://www.mouser.co.uk/ProductDetail/CK/PTS841-ESD-GKP-SMTR-LFS?qs=d0WKAl%252BL4KbeUlwuiSQZWA%3D%3D</a></td><td>0.312</td><td>0.936</td></tr><tr><td>1</td><td>SRV05-4.TCT</td><td>SRV05-4.TCT</td><td>SOT95P280X145-6N</td><td>D2</td><td>USB TVS Diode ESD Suppressor</td><td>Semtech</td><td>SRV05-4.TCT</td><td><a href="https://www.mouser.co.uk/ProductDetail/Semtech/SRV05-4.TCT?qs=rBWM4%252BvDhIe0tfPjqKjR5Q%3D%3D">https://www.mouser.co.uk/ProductDetail/Semtech/SRV05-4.TCT?qs=rBWM4%252BvDhIe0tfPjqKjR5Q%3D%3D</a></td><td>0.808</td><td>0.808</td></tr><tr><td>1</td><td>TCAN1462VDRQ1</td><td>TCAN1462VDRQ1</td><td>SOIC127P600X175-8N</td><td>CAN_T</td><td>CAN FD transceiver</td><td>Texas Instruments</td><td>TCAN1462VDRQ1</td><td><a href="https://www.mouser.co.uk/ProductDetail/Texas-Instruments/TCAN1462VDRQ1?qs=rQFj71Wb1eU28cwJFt9kYg%3D%3D">https://www.mouser.co.uk/ProductDetail/Texas-Instruments/TCAN1462VDRQ1?qs=rQFj71Wb1eU28cwJFt9kYg%3D%3D</a></td><td>1.63</td><td>1.63</td></tr><tr><td>1</td><td>TPS2110APWR</td><td>TPS2110APWR</td><td>SOP65P640X120-8N</td><td>IC2</td><td>Autoswitching Power Mux</td><td>Texas Instruments</td><td>TPS2110APWR</td><td><a href="https://www.mouser.co.uk/ProductDetail/Texas-Instruments/TPS2110APWR?qs=ojKcPFmCWSW5gmLyPB8quA%3D%3D">https://www.mouser.co.uk/ProductDetail/Texas-Instruments/TPS2110APWR?qs=ojKcPFmCWSW5gmLyPB8quA%3D%3D</a></td><td>1.3</td><td>1.3</td></tr><tr><td>1</td><td>TYPE-C-31-M-12</td><td>TYPE-C-31-M-12</td><td>HRO_TYPE-C-31-M-12</td><td>J2</td><td>USB Type C Connector (JLCPCB Assembled)</td><td>HRO Electronics Co.</td><td>TYPE-C-31-M-12</td><td><a href="https://jlcpcb.com/partdetail/Korean_HropartsElec-TYPE_C_31_M12/C165948">https://jlcpcb.com/partdetail/Korean_HropartsElec-TYPE_C_31_M12/C165948</a></td><td>0.157</td><td>0.157</td></tr><tr><td>1</td><td>XW4K-04A1-V1CONN_XW4K-04A1_OMR</td><td>XW4K-04A1-V1CONN_XW4K-04A1_OMR</td><td>CONN_XW4K-04A1_OMR</td><td>J3</td><td>Pluggable Terminal Block 4 pin Vertical Port</td><td>Omron</td><td>XW4K-04A1-V1</td><td><a href="https://www.mouser.co.uk/ProductDetail/Omron-Electronics/XW4K-04A1-V1?qs=wYonFgBYHKlPZJOhR4CEXw%3D%3D&#x26;countryCode=GB&#x26;currencyCode=GBP&#x26;_gl=1*1bs521v*_ga*ODY2MzE2ODU2LjE2ODk3MDQzMTM.*_ga_1KQLCYKRX3*MTcwODMzMjk4NS4xMi4xLjE3MDgzMzI5ODguMC4wLjA.*_ga_15W4STQT4T*MTcwODMzMjk4NS4yOC4xLjE3MDgzMzI5ODguNTcuMC4w">https://www.mouser.co.uk/ProductDetail/Omron-Electronics/XW4K-04A1-V1?qs=wYonFgBYHKlPZJOhR4CEXw%3D%3D&#x26;countryCode=GB&#x26;currencyCode=GBP&#x26;_gl=1*1bs521v*_ga*ODY2MzE2ODU2LjE2ODk3MDQzMTM.*_ga_1KQLCYKRX3*MTcwODMzMjk4NS4xMi4xLjE3MDgzMzI5ODguMC4wLjA.*_ga_15W4STQT4T*MTcwODMzMjk4NS4yOC4xLjE3MDgzMzI5ODguNTcuMC4w</a></td><td>1.79</td><td>1.79</td></tr><tr><td>1</td><td>XW4H-04A1</td><td>XW4H-04A1</td><td>XW4H-04A1</td><td>N/A</td><td>Pluggable Terminal Blocks PCB Terminal Block Wire Side, 4 con</td><td>Omron</td><td>XW4H-04A1</td><td><a href="https://www.mouser.co.uk/ProductDetail/Omron-Electronics/XW4H-04A1?qs=gqBM4hNBiUXOkrvf5L3rEA%3D%3D&#x26;countryCode=GB&#x26;currencyCode=GBP&#x26;_gl=1*1d1by1q*_ga*ODY2MzE2ODU2LjE2ODk3MDQzMTM.*_ga_15W4STQT4T*MTcwODMzMjk4NS4yOC4xLjE3MDgzMzI5OTEuNTQuMC4w*_ga_1KQLCYKRX3*MTcwODMzMjk4NS4xMi4xLjE3MDgzMzI5OTEuMC4wLjA">https://www.mouser.co.uk/ProductDetail/Omron-Electronics/XW4H-04A1?qs=gqBM4hNBiUXOkrvf5L3rEA%3D%3D&#x26;countryCode=GB&#x26;currencyCode=GBP&#x26;_gl=1*1d1by1q*_ga*ODY2MzE2ODU2LjE2ODk3MDQzMTM.*_ga_15W4STQT4T*MTcwODMzMjk4NS4yOC4xLjE3MDgzMzI5OTEuNTQuMC4w*_ga_1KQLCYKRX3*MTcwODMzMjk4NS4xMi4xLjE3MDgzMzI5OTEuMC4wLjA</a>.</td><td>3.05</td><td>3.05</td></tr><tr><td>1</td><td>PMEG3010EJ</td><td>PMEG3010EJ</td><td>SOD-323</td><td>D3</td><td>Schottky Rectifier, 10 V, 2 A, Single, SOD-323, 2 Pins</td><td>NEXPERIA</td><td></td><td><a href="https://www.mouser.co.uk/ProductDetail/Nexperia/PMEG3010EJ115?qs=LOCUfHb8d9u%252Bcs3tLvEEcA%3D%3D">https://www.mouser.co.uk/ProductDetail/Nexperia/PMEG3010EJ115?qs=LOCUfHb8d9u%252Bcs3tLvEEcA%3D%3D</a></td><td>0.328</td><td>0.328</td></tr><tr><td></td><td></td><td></td><td></td><td></td><td></td><td></td><td></td><td></td><td>TOTAL</td><td>25.0872667</td></tr></tbody></table>
{% endtab %}
{% endtabs %}

Some tips on soldering the receiver,

* Start with the bottom surface with the slide switch
* Progress to the other small components (capacitors and resistors)
* Place large components before placing the smaller ones around it (e.g. CAN transceiver before its capacitors)
* On the top side, place the LED first, then the pushbutton switches, then the SD socket, then the CAN termination switch, then the Power switch, then the SMA connector, then the MCU chip, then the Omron connector and finally the JST-XH connector.

## Sensors

#### IMU

The IMU shield uses the Bosch BNO055 breakout board from Adafruit, soldered onto a shield board.

It is the simplest of the sensor shields, showcasing its use case with a typical sensor breakout board.

&#x20;The shield only connects the power lines (5V and GND) as well as the I2C communication lines (SDA and SCL) of the sensor to the node computer.

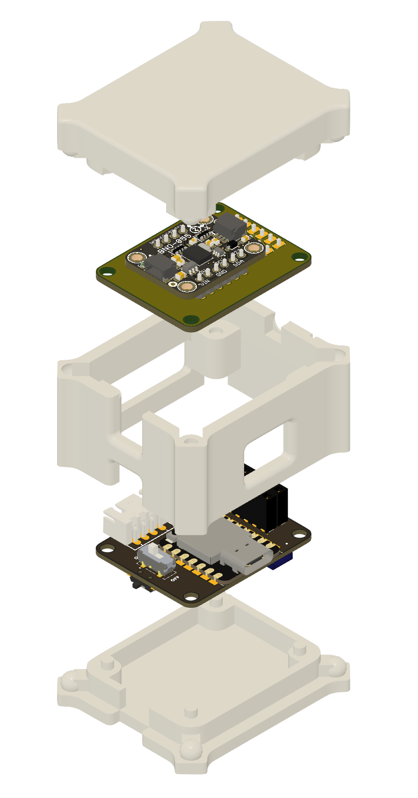
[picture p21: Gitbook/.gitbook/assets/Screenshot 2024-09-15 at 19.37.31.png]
<figure><figcaption><p>Exploded view of the IMU node, with the sensor shield on top.</p></figcaption></figure>

***

#### GPS

The GPS is not a shield but a breakout board directly connected via the Qwiic connector on both the sensor and node computer. This cable connects the power and I2C lines.

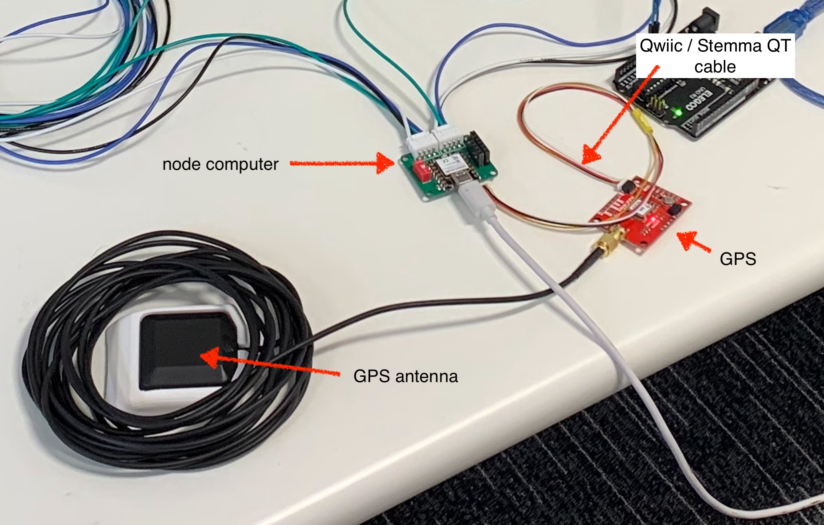
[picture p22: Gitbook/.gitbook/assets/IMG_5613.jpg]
<figure><figcaption><p>Test bench showcasing the GPS connected to the node computer through the Qwiic cable.</p></figcaption></figure>

***
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

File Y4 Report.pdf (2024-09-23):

# Driving Towards Efficiency

## Development of a Live Telemetry System and Driver Interface for UCL Shell Eco Marathon

## Team Members:

## Eric Hsieh

## August Jaubert

## S´andor Otv¨os ¨

## Albert Cristian T˘anase

## Jahanzeb Zahid

## Supervisor: Dr. Llewellyn Morse

Driving towards efficiency

## Acknowledgements

We would like to express our gratitude to our project supervisor, Dr. Llewellyn Morse, for the continuous support throughout the project. His guidance shaped our work ethic to ensure the success of the project. His curiosity and enthusiasm made for exciting meetings and wonderful company. We will cherish the memories created together long past the end of our studies. We would like to thank the teaching staff and our peers at MechSpace for sharing their technical expertise that allowed us to develop a robust product, in particular William Backhouse for his help in developing the electrical circuits. We had a harmonious collaboration with the UCL Shell Eco-Marathon team who integrated us into their family with great warmth. Their help in arranging testing and understanding of the vehicle were key contributors to the project’s development. Last but not least, we would like to thank our families, for their ongoing love and support that allowed us to chase our dreams.

## Abstract

This thesis presents the development of a novel telemetry system designed for an ultra-efficient vehicle competing in the Shell Eco-Marathon. The main goal of the competition is to complete a set number of laps within a given time. The car that manages to do so while using the least amount of energy is declared the winner. The telemetry system aims to provide a platform to record, store and evaluate the prototype’s performance in real time and post-race. The data is transmitted over the bus using a CAN protocol, a racing and automotive standard.

The competition car is subject to design and component changes. As a result, the design process focused on expendability, user-friendliness and robustness, while ensuring cost-effectiveness and energy efficiency. To accommodate these criteria, a modular telemetry system was created, which allows for a rapid and easy integration of additional sensors. The electrical losses and weight of the system were reduced through an iterative process. The development emphasised careful consideration of components with minimal electrical expenditure and high performance. The reduction in circuit size and casing weight was accomplished through custom conformal designs of PCBs and component housings which facilitated the ease of use and robustness of the system.

A telemetry system is meaningful as long as the data can be evaluated and understood by the users. The innovative solution shifts the focus from speed-orientated optimisation, present in the racing industry, to the identification of patterns that lead to the minimisation of energy consumption. As a result, live and post-race analysis platforms have been developed for visualising and interpreting the data. This will aid driver training and the development of the car through three main data streams. The live incoming sensor information is displayed to the driver on an LCD screen which summarises the lap-by-lap performance. In depth data is sent to the race engineer using wireless communication, who will guide the driver in his race performance. Finally, the stored data on the on-board SD-card will be used for analysis using MATLAB that will further deepen the understanding of the car.
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

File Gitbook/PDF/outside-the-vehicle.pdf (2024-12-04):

outside-the-vehicle.md | 2024-12-04

# Outside the vehicle

## Radio Station

Setup

Hardware

1. Assembling the radio station with casing.
2. Attach the radio antenna to the station and USB connector to your laptop.


Software

The radio station uses the Arduino IDE just like the other boards, and will need the RadioHead library installed from the github repository.

Before using the interface two applications need to be installed:

1. MATLAB for using the custom app.
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

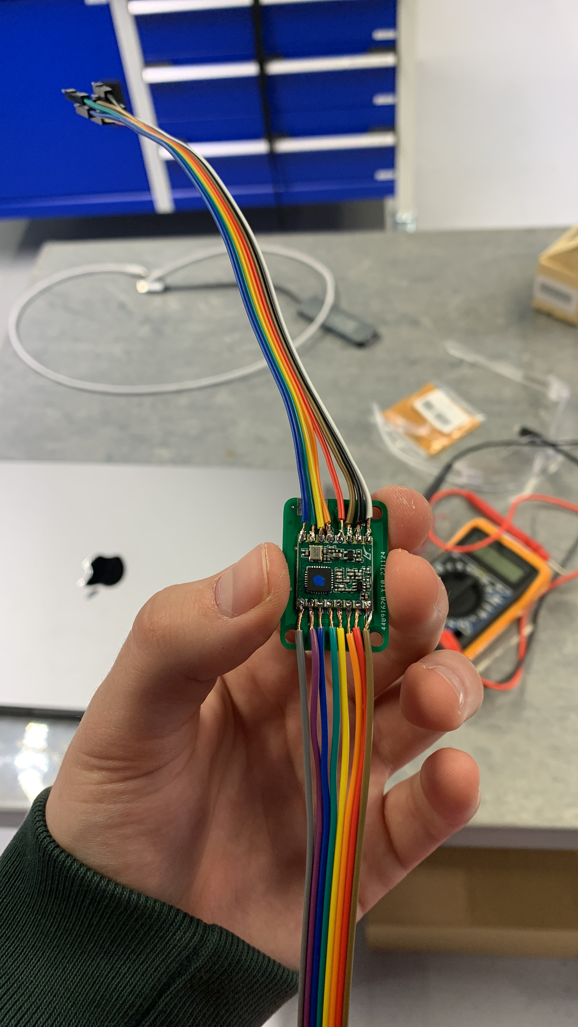
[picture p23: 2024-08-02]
Gitbook/.gitbook/assets/87A55E19-D6DE-48E4-BFD5-C5320AB9867D.JPG

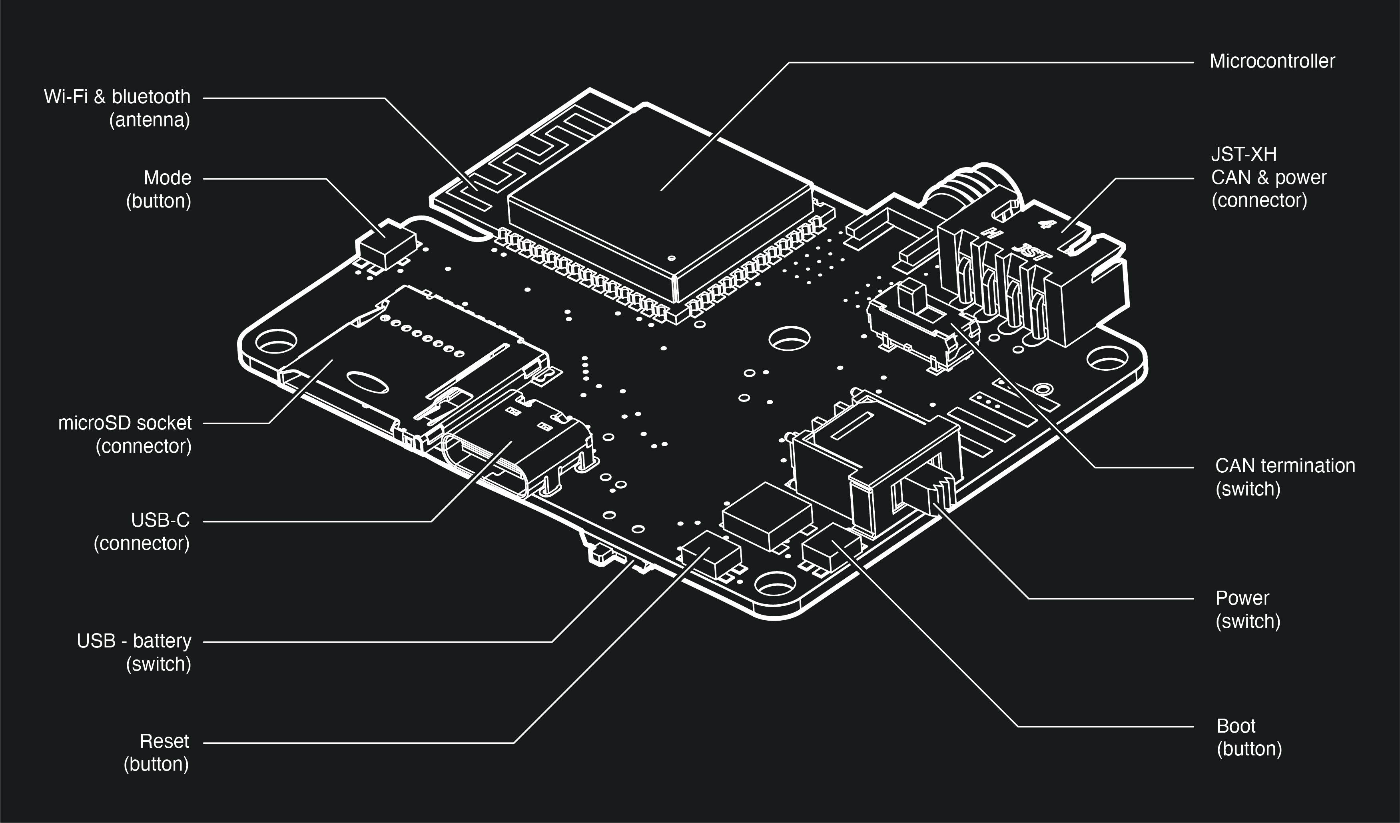
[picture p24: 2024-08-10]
Gitbook/.gitbook/assets/receiver diagram dark@4x.png

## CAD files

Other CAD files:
Hardware/Electronics/Radio station/Fusion files/Radio Station.f3z
Hardware/Electronics/Sensor shields/Display (gen4-IB)/Fusion files/gen4-IB Shield.f3z
Hardware/Electronics/Sensor shields/IMU/Fusion files/BNO055 Shield.f3z
Hardware/Electronics/Sensor shields/RF/Fusion files/RFM69HCW Shield.f3z
Hardware/Electronics/Sensor shields/SD/Fusion files/microSD Shield.f3z
Hardware/Electronics/Sensor shields/Template/Template.f3z

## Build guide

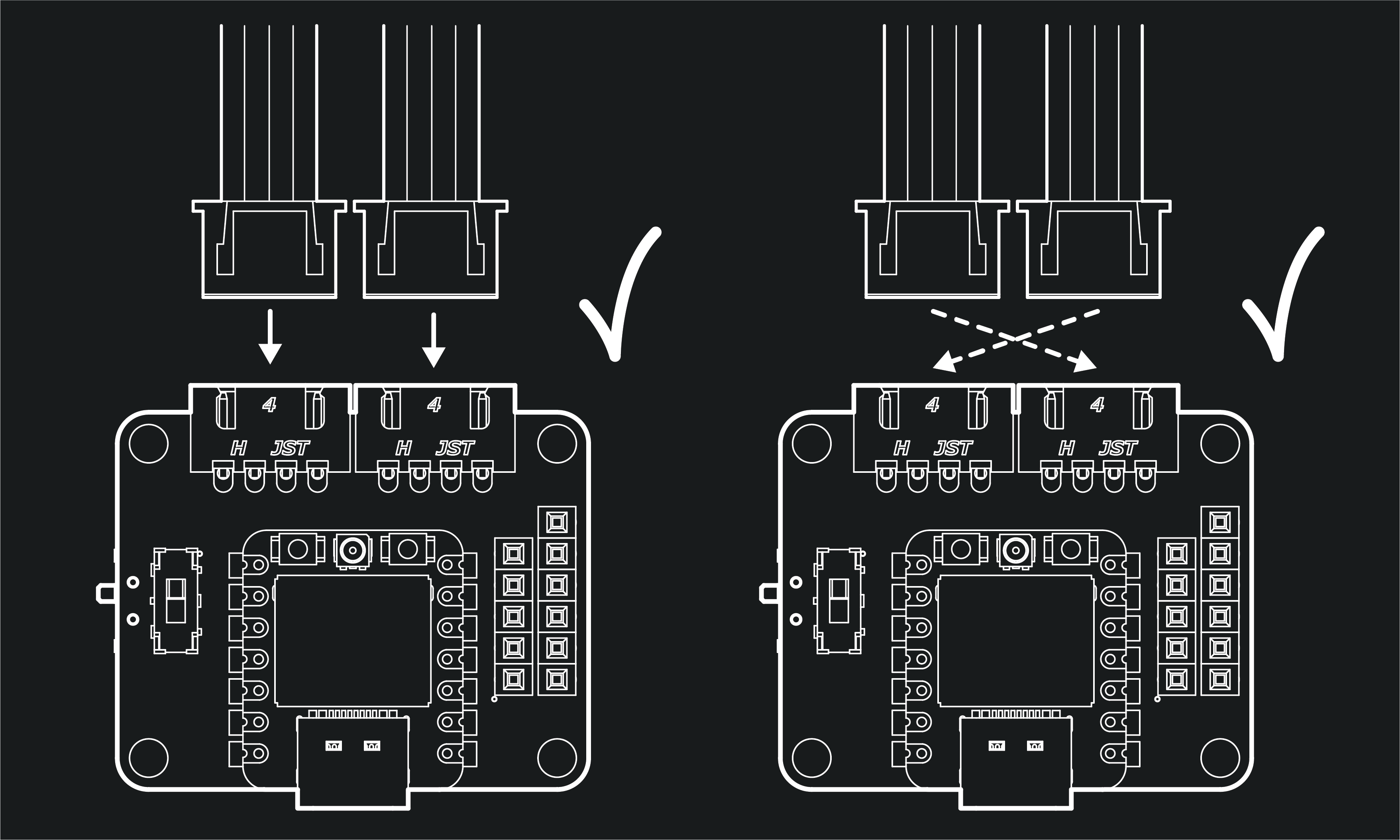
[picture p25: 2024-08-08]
Gitbook/.gitbook/assets/can assembly dark@4x.png

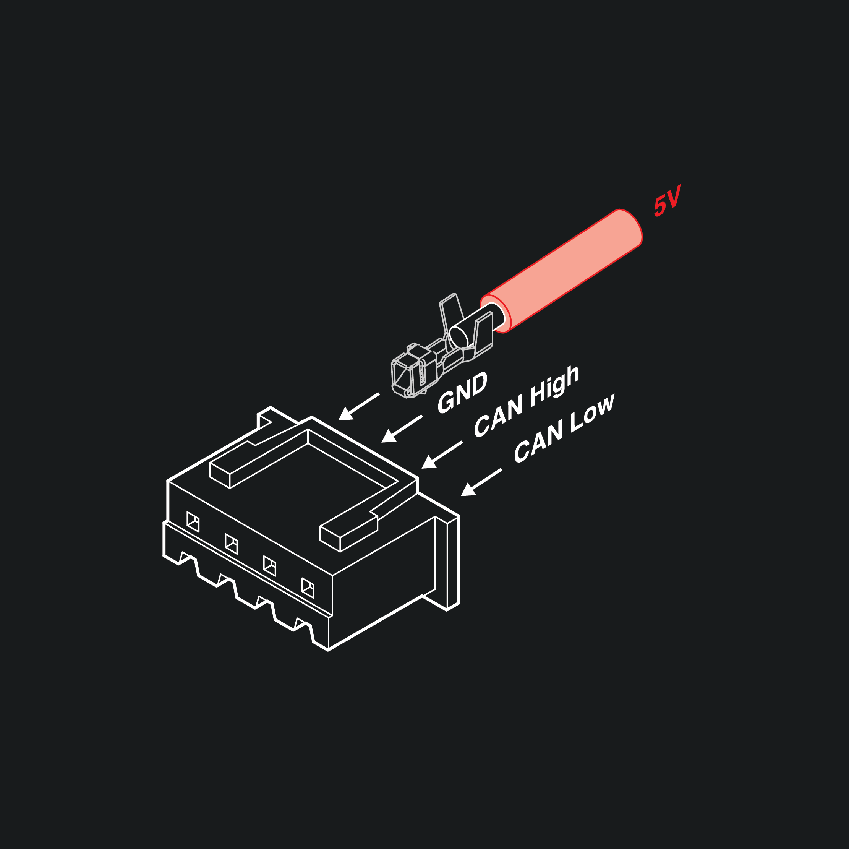
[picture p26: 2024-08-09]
Gitbook/.gitbook/assets/cable wiring dark@4x.png

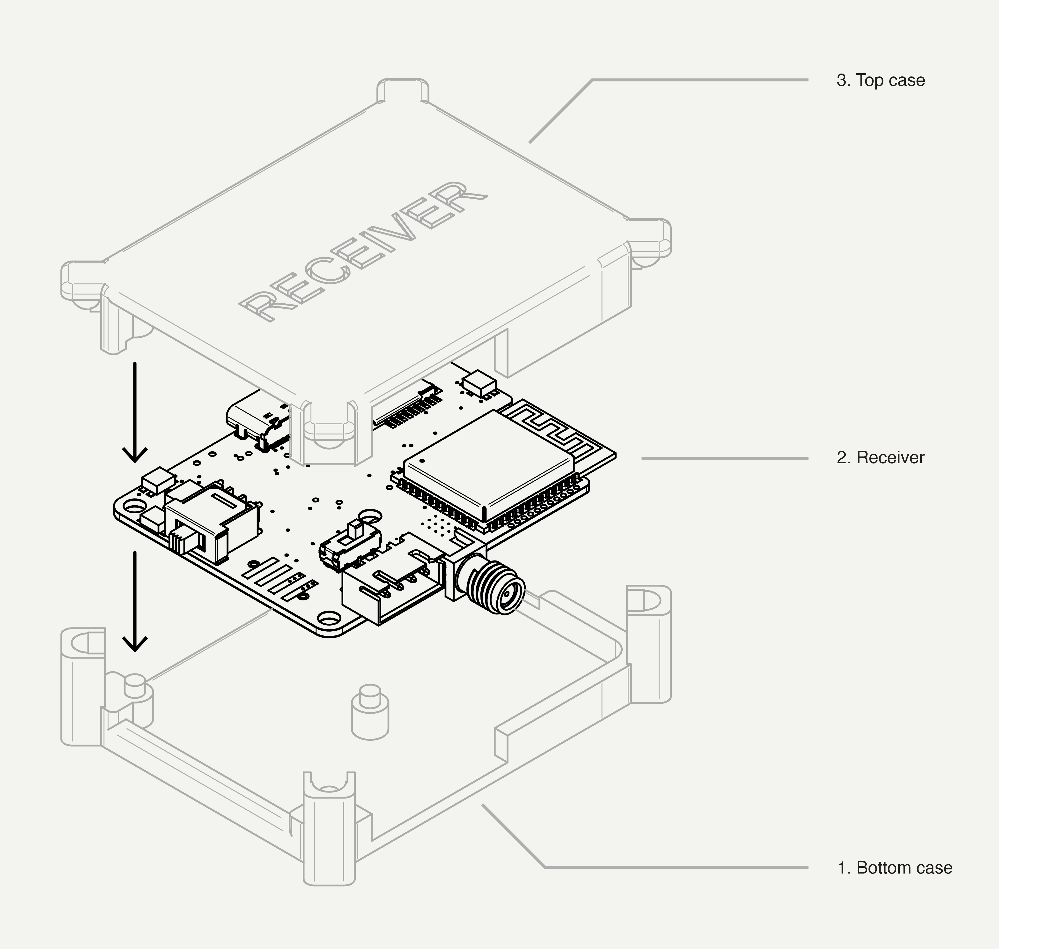
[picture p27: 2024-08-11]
Gitbook/.gitbook/assets/receiver assembly light@4x.png

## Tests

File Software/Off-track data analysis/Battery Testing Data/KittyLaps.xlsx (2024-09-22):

Packet Number | unixTime | Timestamp | Latitude | Longitude | velocity | xAcc | yAcc | zAcc | xNED | yNED | zNED | Throttle | Voltage | Current | Contactor Temp | PCB Temp | Capacity | Power
0 | 0 | 671 | 0 | 0 | 0 | 0 | 0 | 0 | 0 | 0 | 0 | 0 | 0 | 0 | 0 | 0 | 0 | 0
1 | 0 | 751 | 0 | 0 | 0 | 0 | 0 | 0 | 0 | 0 | 0 | 0 | 0 | 0 | 0 | 0 | 0 | 0
2 | 0 | 827 | 0 | 0 | 0 | 0 | 0 | 0 | 0 | 0 | 0 | 0 | 23016 | 0 | 0 | 0 | 0 | 0
3 | 0 | 903 | 0 | 0 | 0 | 0 | 0 | 0 | 0 | 0 | 0 | 0 | 23016 | 0 | 36000 | 22100 | 0 | 0
4 | 0 | 980 | 0 | 0 | 0 | 0 | 0 | 0 | 0 | 0 | 0 | 0 | 23016 | 0 | 36000 | 22100 | 0 | 0
5 | 0 | 1064 | 0 | 0 | 0 | 0 | 0 | 0 | 0 | 0 | 0 | 0 | 23016 | 0 | 36000 | 22100 | 0 | 0
6 | 0 | 1145 | 0 | 0 | 0 | 0 | 0 | 0 | 0 | 0 | 0 | 0 | 23016 | 0 | 36000 | 22100 | 0 | 0
7 | 0 | 1219 | 0 | 0 | 0 | 0 | 0 | 0 | 0 | 0 | 0 | 0 | 23016 | 0 | 36000 | 22100 | 0 | 0
8 | 0 | 1292 | 0 | 0 | 0 | 0 | 0 | 0 | 0 | 0 | 0 | 0 | 23017 | 0 | 36000 | 22100 | 0 | 0
9 | 0 | 1365 | 0 | 0 | 0 | 0 | 0 | 0 | 0 | 0 | 0 | 0 | 23017 | 0 | 35800 | 22100 | 0 | 0
10 | 0 | 1442 | 0 | 0 | 0 | 0 | 0 | 0 | 0 | 0 | 0 | 0 | 23017 | 0 | 35800 | 22100 | 0 | 0
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

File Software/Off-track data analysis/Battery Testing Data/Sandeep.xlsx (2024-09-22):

Lap1 | Unix1 | Voltage | Lap2 | Unix2 | SOC | CAP_Volt | Lap3 | Unix3 | zAcc | Lap4 | Unix4 | xAcc | yAcc | Lap5 | Unix5 | Velocity | Lap6 | Unix6 | Lat | Lon | Lap7 | Unix7 | Curr3 | Curr3 | Lap8 | Unix8 | Curr2 | Curr2_raw | Lap9 | Unix9 | Curr1 | Curr1_raw
0 | 214604 | 0 | 0 | 226723 | 99.75 | 32.32 | 0 | 179809 | -9.75 | 0 | 190535 | 1.33 | 0.11 | 0 | 283243 | 23 | 0 | 309214 | 514203719 | 3492075 | 0 | 150466 | 0 | 50 | 0 | 627145 | 0 | 81 | 0 | 111924 | 0.87 | 358
0 | 966598 | 0 | 0 | 976356 | 99.29 | 32.17 | 0 | 713393 | -9.74 | 0 | 727720 | 1.32 | 0.11 | 0 | 552169 | 5 | 0 | 576788 | 514203721 | 3492074 | 0 | 689446 | 0 | 55 | 0 | 1254126 | 0 | 81 | 0 | 665928 | 0.11 | -34
0 | 1723635 | 0 | 0 | 1735886 | 99.23 | 32.15 | 0 | 1218770 | -9.74 | 0 | 1231861 | 1.31 | 0.11 | 0 | 875242 | 6 | 0 | 904207 | 514203723 | 3492071 | 0 | 1321579 | 0 | 54 | 0 | 1886143 | 0 | 81 | 0 | 1294971 | 0 | -97
0 | 2475671 | 0 | 0 | 2489632 | 99.26 | 32.16 | 0 | 1761882 | -9.74 | 0 | 1776474 | 1.32 | 0.12 | 0 | 1352849 | 70 | 0 | 1371183 | 514203724 | 3492069 | 0 | 1948077 | 0 | 54 | 0 | 2513330 | 0 | 82 | 0 | 1928964 | -0.01 | -100
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

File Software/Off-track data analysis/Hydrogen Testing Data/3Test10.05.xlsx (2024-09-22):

Lap1 | Unix1 | Voltage | Lap2 | Unix2 | SOC | CAP_Volt | Lap3 | Unix3 | zAcc | Lap4 | Unix4 | xAcc | yAcc | Lap5 | Unix5 | Velocity | Lap6 | Unix6 | Lat | Lon | Lap7 | Unix7 | Curr3 | Curr3 | Lap8 | Unix8 | Curr2 | Curr2_raw | Lap9 | Unix9 | Curr1 | Curr1_raw
0 | 430714 | 0 | 0 | 441554 | 3.86 | 1.25 | 0 | 369051 | -9.74 | 0 | 383727 | 1.34 | 0.11 | 0 | 399066 | 11 | 0 | 111893 | 514203625 | 3491989 | 0 | 247893 | 0 | -23 | 0 | 190606 | 0 | 18 | 0 | 223104 | 0 | -111
0 | 1156590 | 0 | 0 | 1170214 | 3.86 | 1.25 | 0 | 890982 | -9.74 | 0 | 902585 | 1.34 | 0.11 | 0 | 641264 | 7 | 0 | 417452 | 514203628 | 3491989 | 0 | 872325 | 0 | -21 | 0 | 817613 | 0 | 18 | 0 | 848634 | 0 | -112
0 | 1913606 | 0 | 0 | 1923373 | 3.83 | 1.24 | 0 | 1427361 | -9.74 | 0 | 1437942 | 1.34 | 0.11 | 0 | 959195 | 12 | 0 | 664860 | 514203630 | 3491989 | 0 | 1502289 | 0 | -22 | 0 | 1449849 | 0 | 17 | 0 | 1476812 | 0 | -111
0 | 2665639 | 0 | 0 | 2679268 | 3.83 | 1.24 | 0 | 1944731 | -9.74 | 0 | 1957748 | 1.33 | 0.11 | 0 | 1391259 | 7 | 0 | 982587 | 514203633 | 3491989 | 0 | 2128994 | 0 | -23 | 0 | 2076645 | 0 | 17 | 0 | 2109675 | 0 | -111
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

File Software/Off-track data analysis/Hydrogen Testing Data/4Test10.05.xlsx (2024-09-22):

Lap1 | Unix1 | Voltage | Lap2 | Unix2 | SOC | CAP_Volt | Lap3 | Unix3 | zAcc | Lap4 | Unix4 | xAcc | yAcc | Lap5 | Unix5 | Velocity | Lap6 | Unix6 | Lat | Lon | Lap7 | Unix7 | Curr3 | Curr3 | Lap8 | Unix8 | Curr2 | Curr2_raw | Lap9 | Unix9 | Curr1 | Curr1_raw
0 | 214604 | 0 | 0 | 226723 | 99.75 | 32.32 | 0 | 179809 | -9.75 | 0 | 190535 | 1.33 | 0.11 | 0 | 283243 | 23 | 0 | 309214 | 514203719 | 3492075 | 0 | 150466 | 0 | 50 | 0 | 627145 | 0 | 81 | 0 | 111924 | 0.87 | 358
0 | 966598 | 0 | 0 | 976356 | 99.29 | 32.17 | 0 | 713393 | -9.74 | 0 | 727720 | 1.32 | 0.11 | 0 | 552169 | 5 | 0 | 576788 | 514203721 | 3492074 | 0 | 689446 | 0 | 55 | 0 | 1254126 | 0 | 81 | 0 | 665928 | 0.11 | -34
0 | 1723635 | 0 | 0 | 1735886 | 99.23 | 32.15 | 0 | 1218770 | -9.74 | 0 | 1231861 | 1.31 | 0.11 | 0 | 875242 | 6 | 0 | 904207 | 514203723 | 3492071 | 0 | 1321579 | 0 | 54 | 0 | 1886143 | 0 | 81 | 0 | 1294971 | 0 | -97
0 | 2475671 | 0 | 0 | 2489632 | 99.26 | 32.16 | 0 | 1761882 | -9.74 | 0 | 1776474 | 1.32 | 0.12 | 0 | 1352849 | 70 | 0 | 1371183 | 514203724 | 3492069 | 0 | 1948077 | 0 | 54 | 0 | 2513330 | 0 | 82 | 0 | 1928964 | -0.01 | -100
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

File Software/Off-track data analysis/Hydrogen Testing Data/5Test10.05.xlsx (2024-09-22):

Lap1 | Unix1 | Voltage | Lap2 | Unix2 | SOC | CAP_Volt | Lap3 | Unix3 | zAcc | Lap4 | Unix4 | xAcc | yAcc | Lap5 | Unix5 | Velocity | Lap6 | Unix6 | Lat | Lon | Lap7 | Unix7 | Curr3 | Curr3 | Lap8 | Unix8 | Curr2 | Curr2_raw | Lap9 | Unix9 | Curr1 | Curr1_raw
0 | 752118 | 0 | 0 | 111926 | 99.01 | 32.08 | 0 | 491539 | -9.82 | 0 | 504731 | 1.22 | 0.14 | 0 | 321362 | 24 | 0 | 347090 | 514203572 | 3492475 | 0 | 470160 | 0 | 58 | 0 | 413334 | 0 | 78 | 0 | 451227 | 0 | -92
0 | 1509112 | 0 | 0 | 766027 | 98.95 | 32.06 | 0 | 1001275 | -9.74 | 0 | 1014520 | 1.33 | 0.12 | 0 | 593594 | 44 | 0 | 618472 | 514203573 | 3492473 | 0 | 1106918 | -0.01 | 52 | 0 | 1040305 | 0 | 81 | 0 | 1080171 | 1.24 | 553
0 | 2261132 | 0 | 0 | 1519242 | 99.6 | 32.27 | 0 | 1546473 | -9.72 | 0 | 1559888 | 1.34 | 0.11 | 0 | 918635 | 31 | 0 | 937049 | 514203573 | 3492468 | 0 | 1733529 | 0 | 58 | 0 | 1672360 | -0.01 | 76 | 0 | 1714251 | 0.03 | -70
0 | 3043762 | 0 | 0 | 2275183 | 99.04 | 32.09 | 0 | 2039266 | -9.76 | 0 | 2054116 | 1.35 | 0.13 | 0 | 1290683 | 19 | 0 | 1309353 | 514203573 | 3492466 | 0 | 2379832 | -0.01 | 56 | 0 | 2299395 | 0 | 79 | 0 | 2354789 | -0.03 | -105
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

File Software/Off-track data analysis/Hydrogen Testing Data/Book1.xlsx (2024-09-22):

 | August | Mattias | Albert | Total |  | Total August | Total Mattias | Total Albert | Total
Airport Breakfast | £8.75 | £15.00 | £21.00 | £44.75 | Euro | €50.28 | €69.46 | €85.11 | €204.85
Nearys Lunch | €6.80 | €6.80 | €12.00 | €25.60 | Pounds | £13.60 | £41.10 | £25.85 | €80.55
Uber to Little Dublin | £4.85 | £4.85 | £4.85 | £14.55 | Total in Pounds | £56.06 | £99.76 |  | £155.82
Laragh Inn | €18.75 | €10.50 | €21.95 | €51.20
Kish Fish | €0.00 | €19.42 | €23.42 | €42.85
Uber from Howth | €22.07 | €22.07 | €22.07 | €66.20
Airport Gifts | €2.67 | €10.67 | €5.67 | €19.00
Trainline |  | £21.25 | £21.25 | £42.50

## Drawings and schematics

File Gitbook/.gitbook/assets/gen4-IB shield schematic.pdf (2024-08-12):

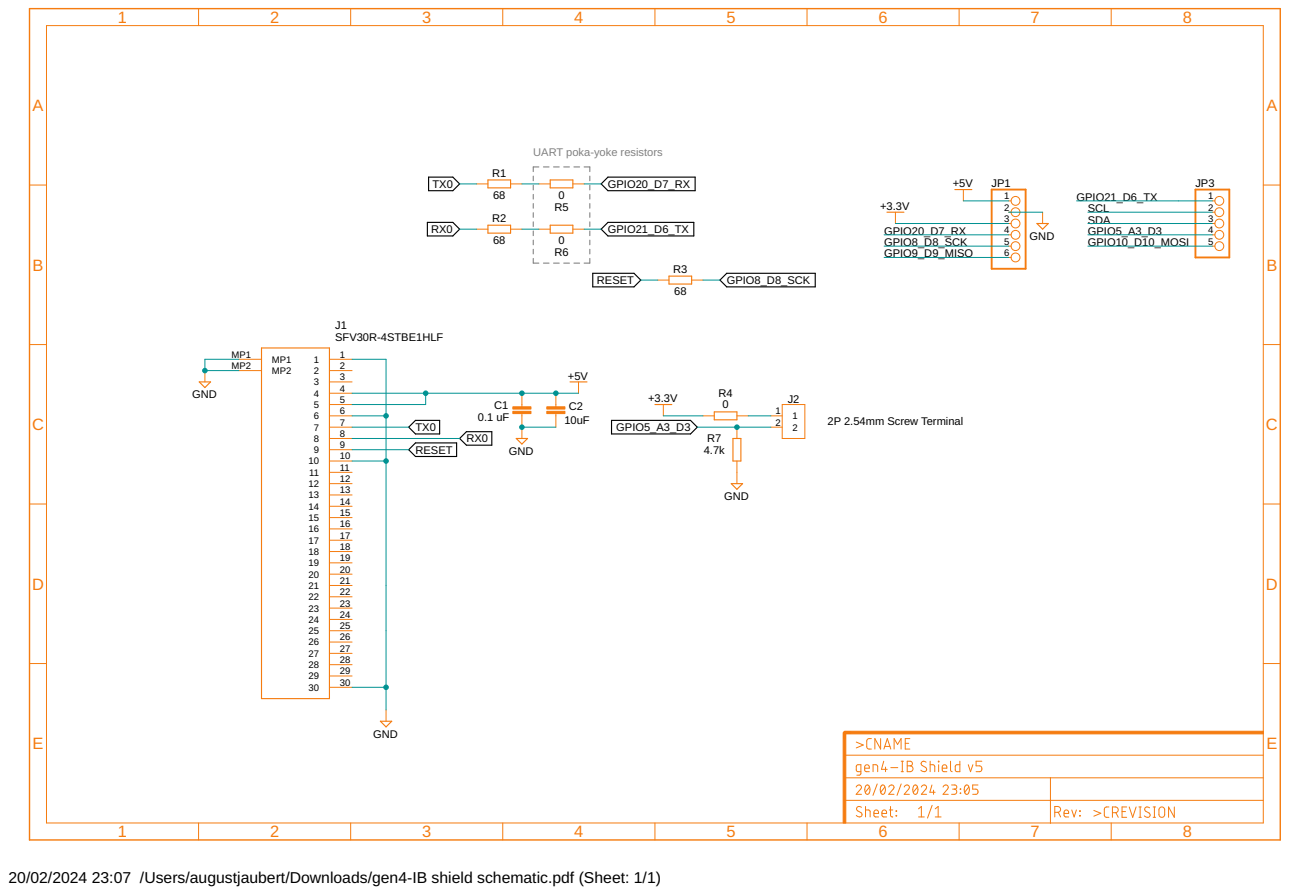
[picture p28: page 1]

20/02/2024 23:07 /Users/augustjaubert/Downloads/gen4-IB shield schematic.pdf (Sheet: 1/1)

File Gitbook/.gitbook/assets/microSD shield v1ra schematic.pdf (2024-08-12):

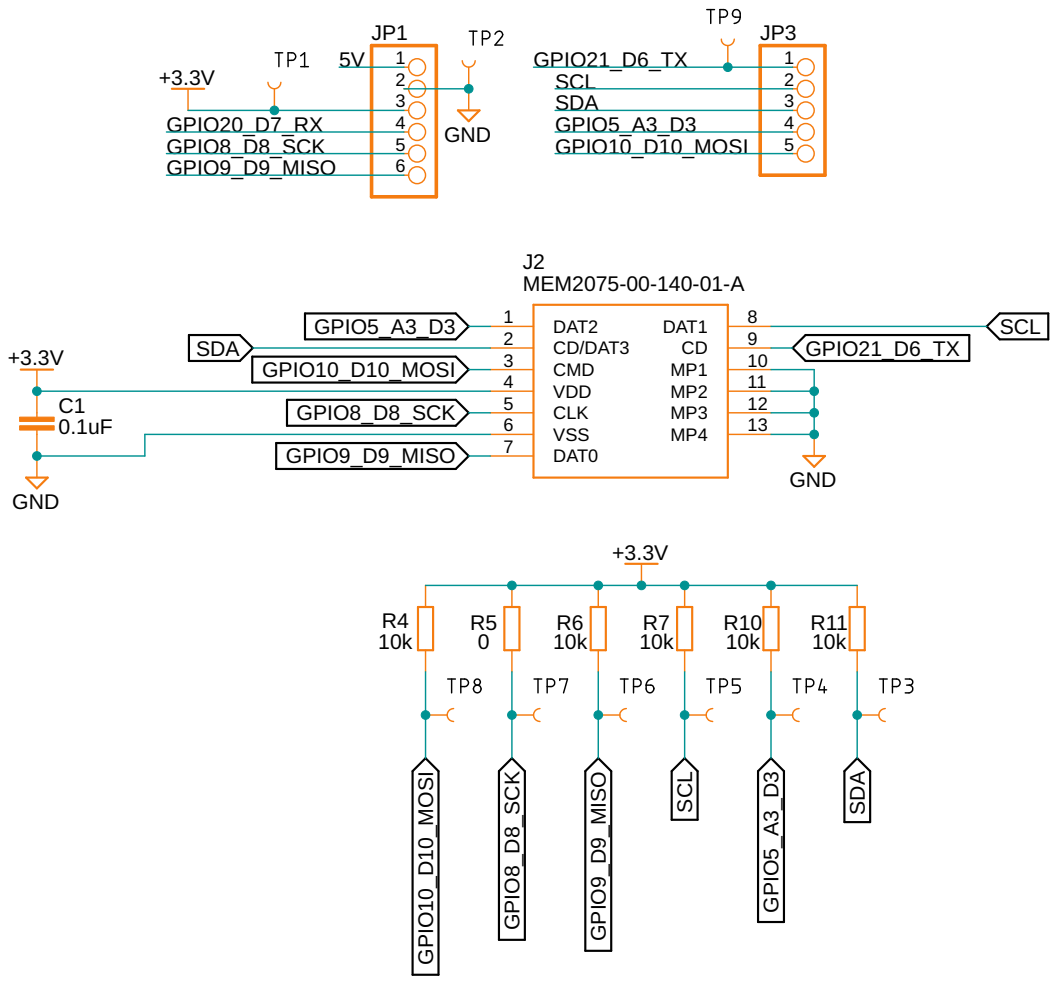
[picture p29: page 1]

GPIO5_A3_D3 | DAT1 VDD | 8 CD 9 MP1

SDA | | GPIO21_D6_TX

20/02/2024 16:24 /Users/augustjaubert/Downloads/microSD shield schematic.pdf (Sheet: 1/1)

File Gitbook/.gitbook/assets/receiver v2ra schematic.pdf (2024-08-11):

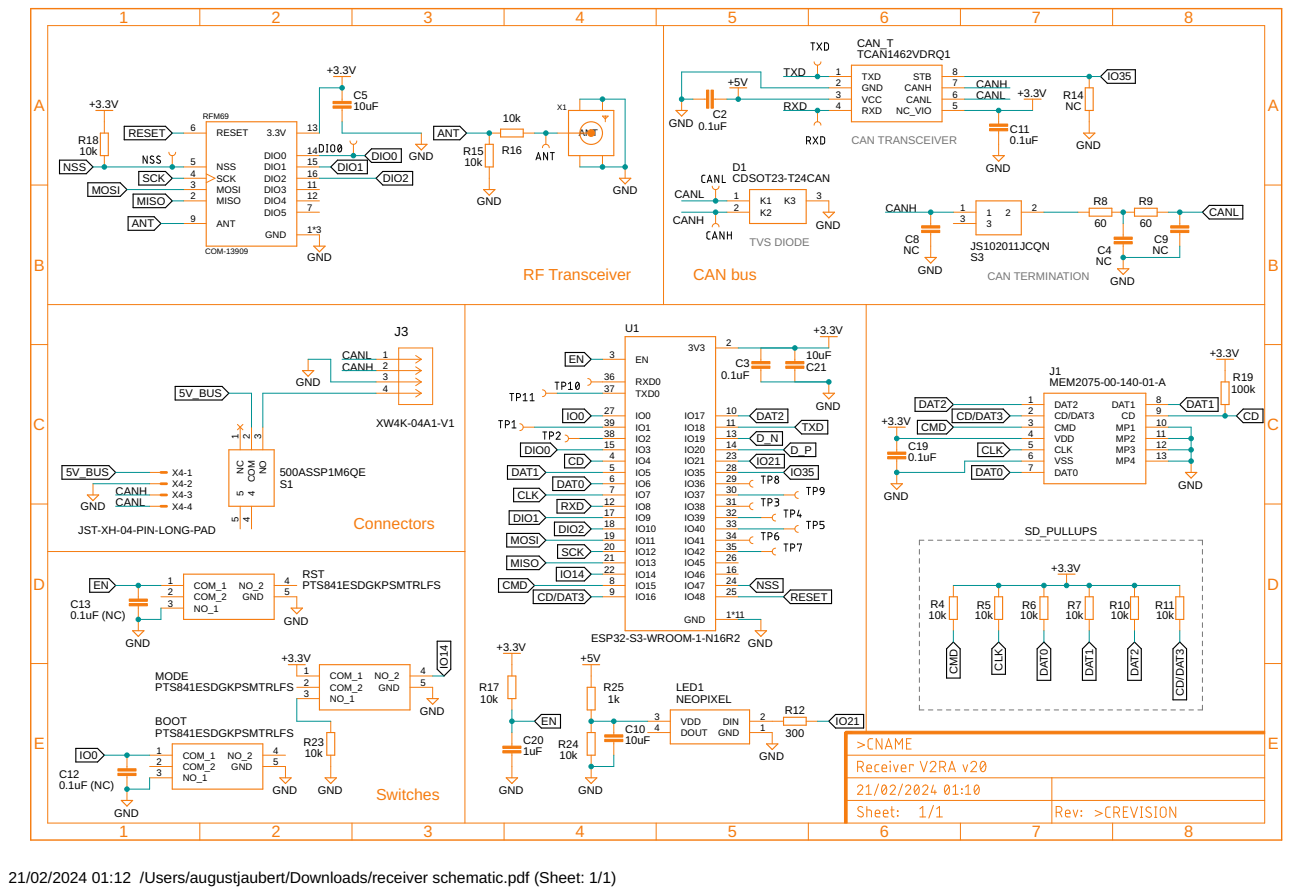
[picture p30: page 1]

+3.3V | | | TCAN1462VDRQ1

CANH
CANL
GND
JST-XH-04-PIN-LONG-PAD

21/02/2024 01:12 /Users/augustjaubert/Downloads/receiver schematic.pdf (Sheet: 1/1)

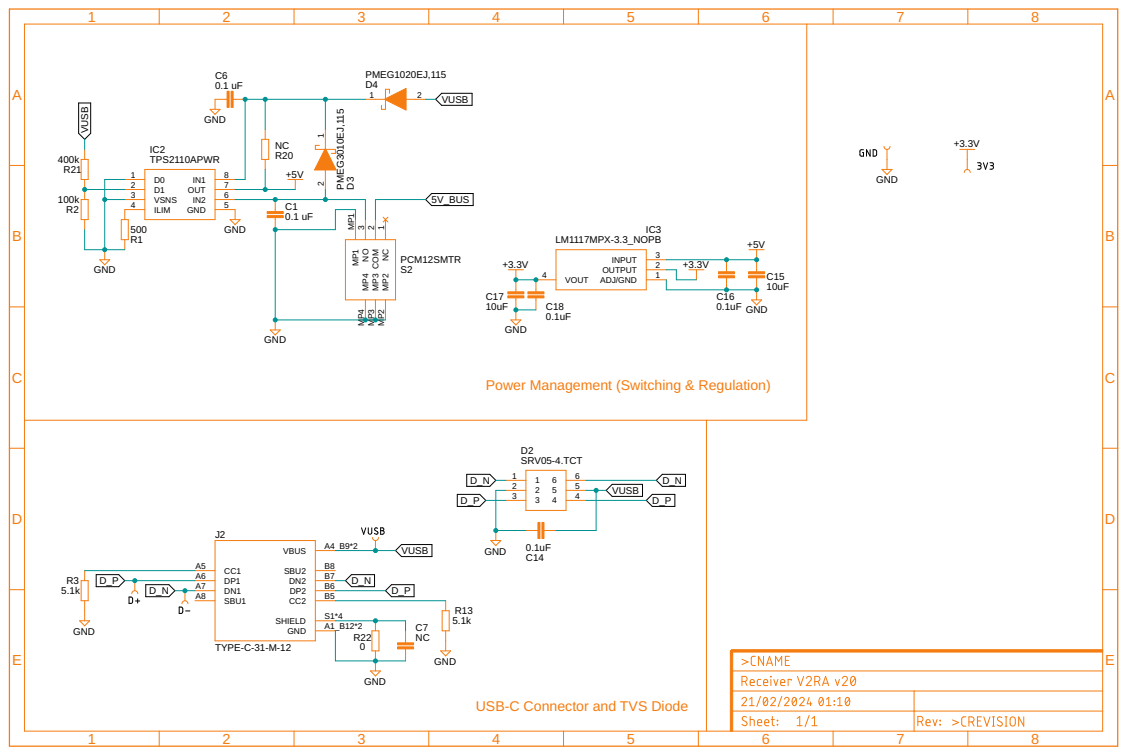
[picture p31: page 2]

C6 PMEG1020EJ,115 D4 0.1 uF

Power Management (Switching & Regulation)

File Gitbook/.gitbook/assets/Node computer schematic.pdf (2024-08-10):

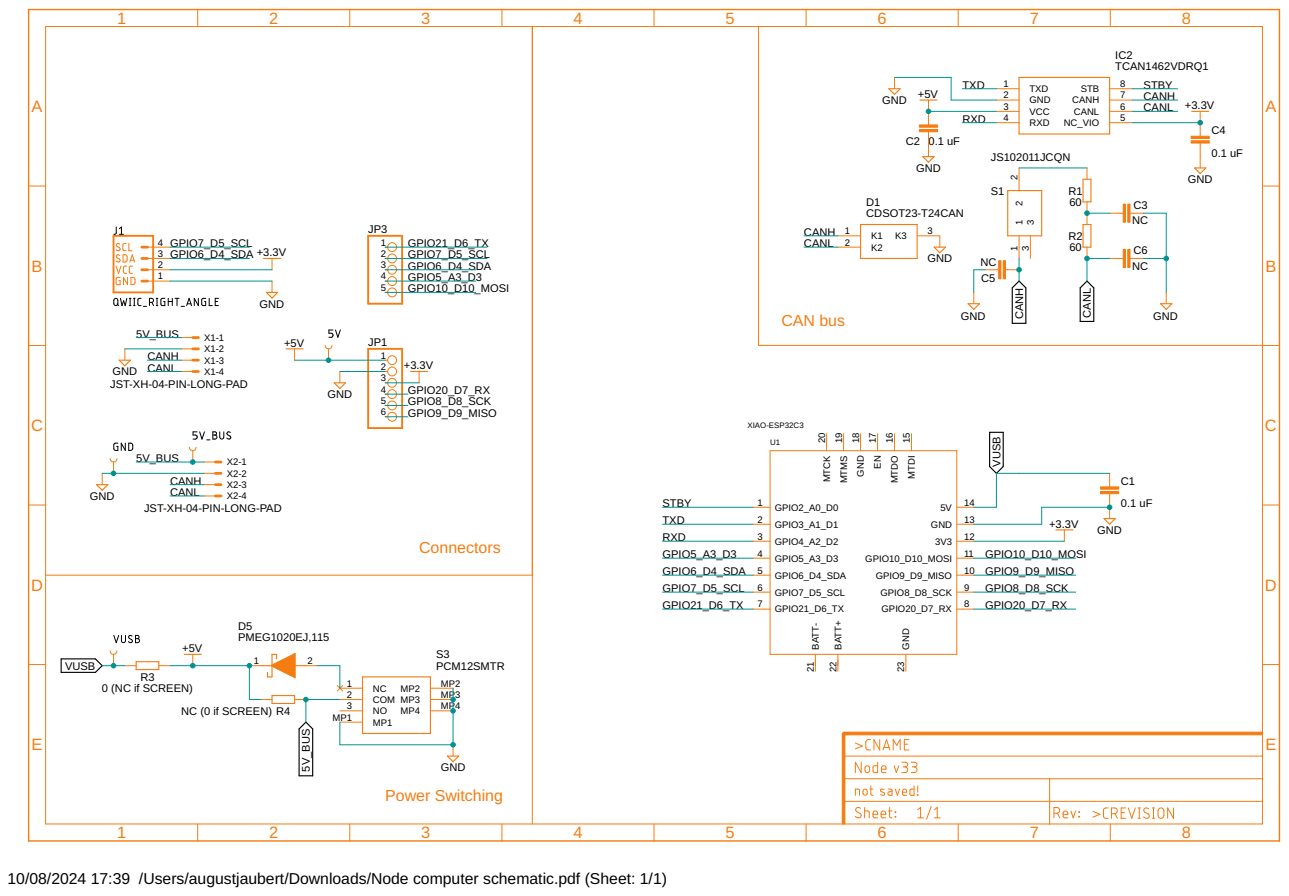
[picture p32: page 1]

IC2 TCAN1462VDRQ1

10/08/2024 17:39 /Users/augustjaubert/Downloads/Node computer schematic.pdf (Sheet: 1/1)

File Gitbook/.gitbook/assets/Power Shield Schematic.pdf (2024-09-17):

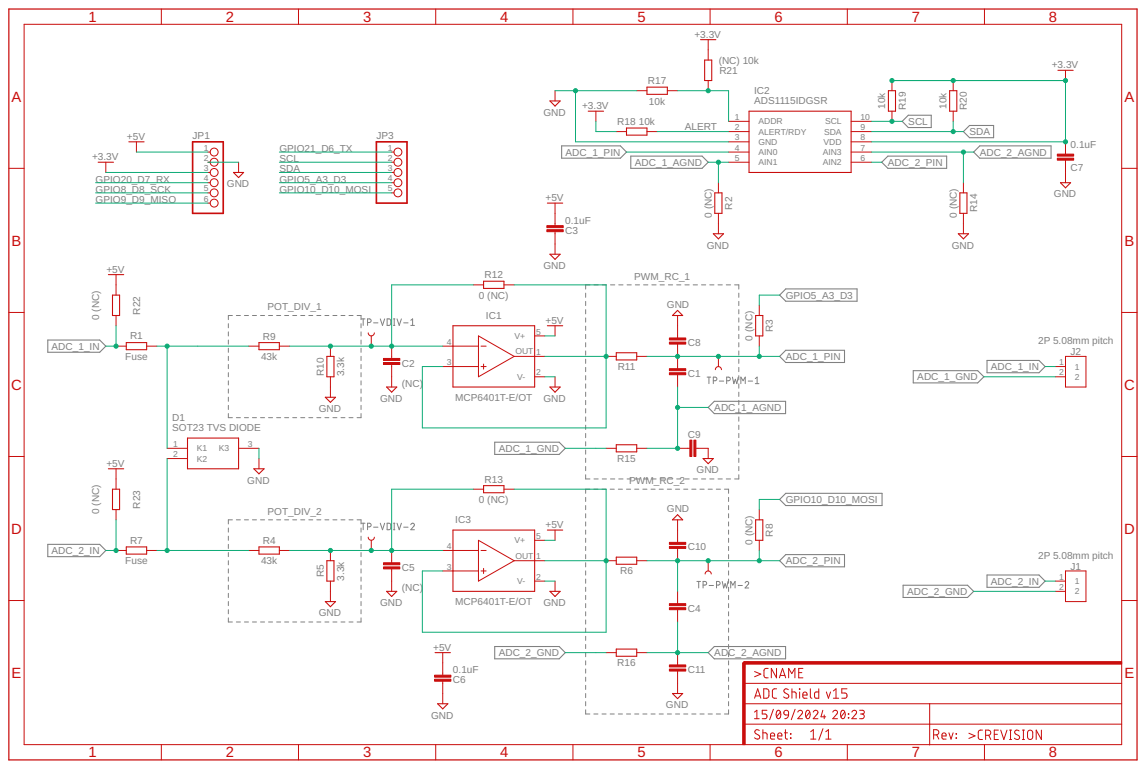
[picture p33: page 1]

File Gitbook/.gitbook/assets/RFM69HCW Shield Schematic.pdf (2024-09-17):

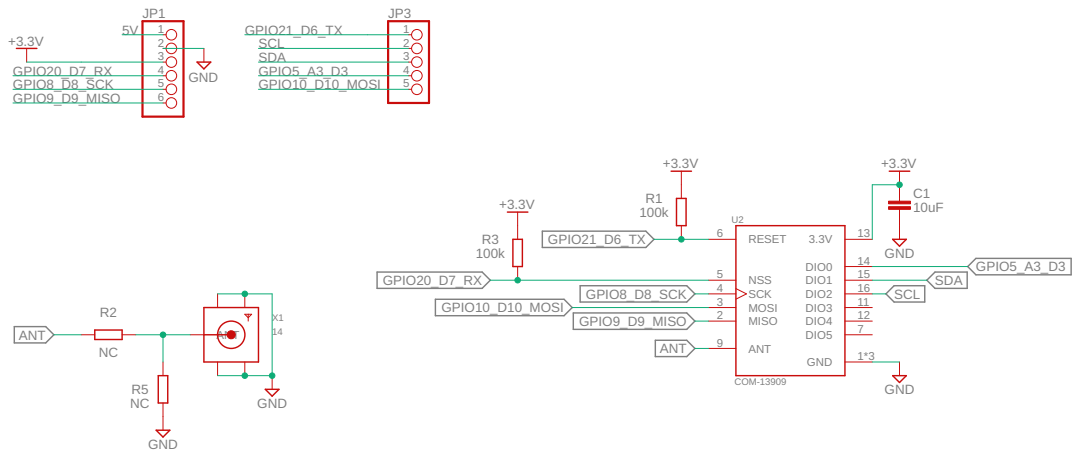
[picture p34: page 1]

15 DIO2

GPIO8_D8_SCK | SCL
